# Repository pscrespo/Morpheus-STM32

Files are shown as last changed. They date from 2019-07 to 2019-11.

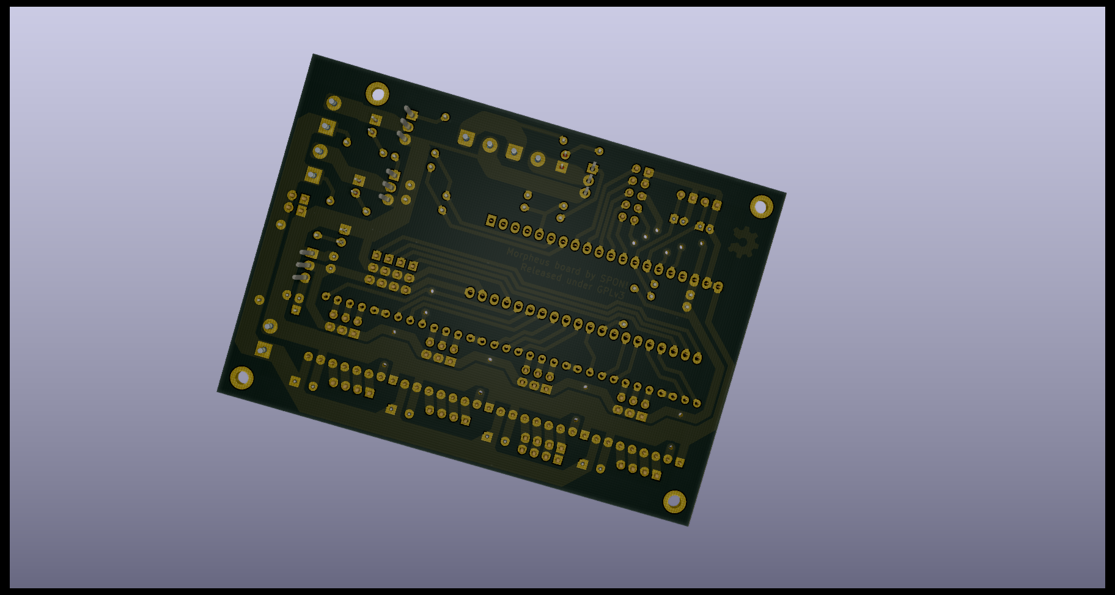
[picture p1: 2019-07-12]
documents/render3.png

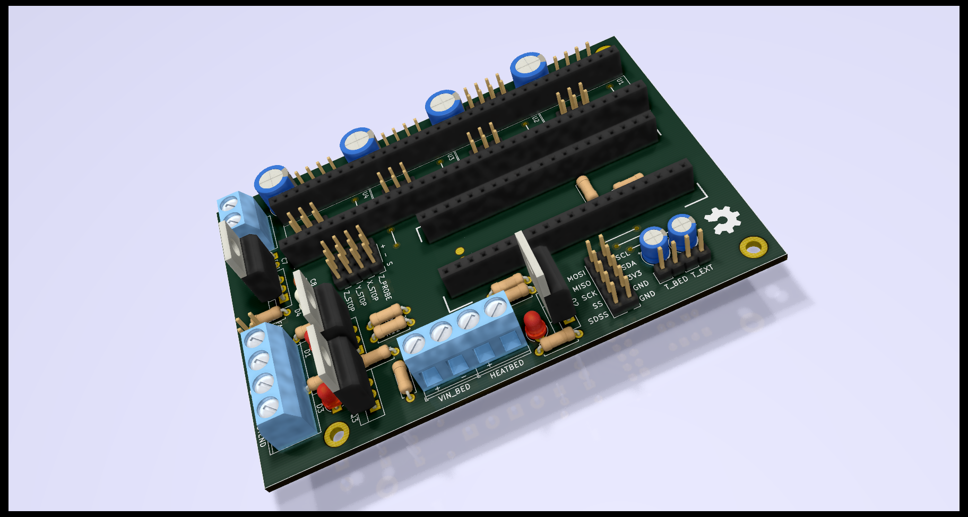
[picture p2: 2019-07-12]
documents/render2.png

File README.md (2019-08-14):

# Morpheus-STM32 (work in progress)
A cheap 3D printer controller board for use with a "Blue Pill" STM32F1 generic board. Inspired on http://reprap.org/wiki/SinapTec

Design goals:
---------------

 - Follow the [KISS Principle](https://en.wikipedia.org/wiki/KISS_principle)
 - Low cost
 - Single layer copper board
 - DIY-able (easy to make via toner transfer)
 - Only through-hole components
 - The very basic a printer would need
   - Keep bed circuit separated/optional (if you are making a PLA only printer without a heated bed, you don't need to populate the bed circuit zone)
 - Open Source Hardware, made in Open Source Software

Features:
---------------

 - 4 Pololu-like steppers (X, Y, Z, E0)
 - 3 mosfets (Hotend heater, print cooling fan and bed heater)
 - 3 MIN endstops (X, Y, Z)
 - Z Probe pin (in case you are building a delta printer and need the extra endstop)
 - 2 thermistors (for E0 and bed)
 - 2 12V fan connectors
 - I2C and SPI header
  
 # WARNING:
 - All logic voltage in this board is 3.3V. Do not connect 5V logic addons/devices without proper level adapting.
 - ~This board has no reverse current protection,~ it has a diode to short-circuit and protect the board in case of reverse current, but if you connect power incorrectly you'll still damage components and/or your power supply (there's also a risk of caching fire, so please be careful).
 - This board has no overcurrent protection, please use a fuse on power input (e.g. auto-blade or inline fuse holder), recommended values are of 5A for the main board and 10A for the bed circuit.
 - Check all connections before plugging power.
 - Now for real, check connections...
 
 Notes:
 ---------------
 - Usually, "blue pill" boards have a wrong R10 value (USB pullpup resistor, should be 1.5k but manufcturers place a 10k or other value resistor instead), so you can add a 1.8k in R13. If your board has the correct value or you already fixed it in the board, then leave R13 unpopulated.
 - ~Hotend sensor uses a 1k resistor pullup (R1). Anyway, if you're having trouble with finding (or creating) thermistor tables, just replace it with a 4.7k resistor and use the usual Marlin tables.~ 
  Now Marlin has configurable thermistors, you can use thermistor **1000** in **configuration.h** and choose pull-up, ressistance and beta values in **configuration_adv.h**

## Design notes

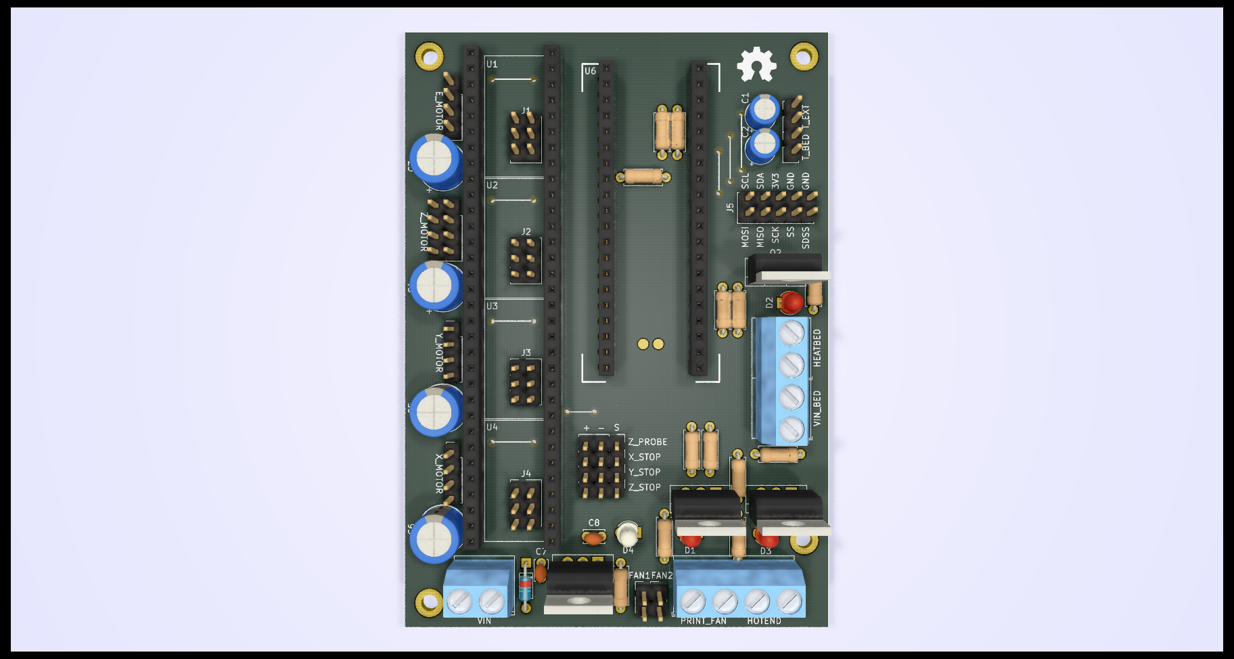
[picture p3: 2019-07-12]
documents/render1.png

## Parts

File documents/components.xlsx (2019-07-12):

Reference | Quantity | Value | Footprint | Notes
C1 C2 | 2 | 10uF10v | Capacitor_THT:CP_Radial_D5.0mm_P2.00mm
C3 C4 C5 C6 | 4 | 470uF16v | Capacitor_THT:CP_Radial_D8.0mm_P3.80mm
C7 C8 | 2 | 0.1uF | Capacitor_THT:C_Disc_D3.4mm_W2.1mm_P2.50mm
D1 D2 D3 | 3 | LED 3mm (Red) | LED_THT:LED_D3.0mm
D4 | 1 | LED 3mm (Green) | LED_THT:LED_D3.0mm_Clear
D5 | 1 | 1N4007 | Diode_THT:D_DO-35_SOD27_P7.62mm_Horizontal
HEATBED1 HOTEND1 PRINT_FAN1 VIN1 VIN_BED1 | 5 | Phoenix MKDS-1,5 2pin | TerminalBlock_Phoenix:TerminalBlock_Phoenix_MKDS-1,5-2_1x02_P5.00mm_Horizontal
Q1 Q3 | 2 | IRLZ44N | Package_TO_SOT_THT:TO-220-3_Vertical
Q2 | 1 | IRLB3034PBF | Package_TO_SOT_THT:TO-220-3_Vertical
R1 R3 R6 R9 | 4 | 1K | Resistor_THT:R_Axial_DIN0207_L6.3mm_D2.5mm_P7.62mm_Horizontal
R12 R2 | 2 | 4K7 | Resistor_THT:R_Axial_DIN0207_L6.3mm_D2.5mm_P7.62mm_Horizontal
R13 | 1 | 1K8 | Resistor_THT:R_Axial_DIN0207_L6.3mm_D2.5mm_P7.62mm_Horizontal | May be a different value for your bluepill, or not even needed.
R10 R4 R7 | 3 | 10R | Resistor_THT:R_Axial_DIN0207_L6.3mm_D2.5mm_P7.62mm_Horizontal
R11 R5 R8 | 3 | 100K | Resistor_THT:R_Axial_DIN0207_L6.3mm_D2.5mm_P7.62mm_Horizontal
T_BED1 T_EXT1 FAN1 FAN2 | 4 | Male header 01x02 | Connector_PinHeader_2.54mm:PinHeader_1x02_P2.54mm_Vertical | There are 74 pins in total, so you need 2 40pin header strips.
J1 J2 J3 J4 | 4 | Male header 02x03 | Connector_PinHeader_2.54mm:PinHeader_2x03_P2.54mm_Vertical
J5 | 1 | Male header 02x05 | Connector_PinHeader_2.54mm:PinHeader_2x05_P2.54mm_Vertical
X_STOP1 Y_STOP1 Z_STOP1 Z_PROBE1 | 4 | Male header 01x03 | Connector_PinHeader_2.54mm:PinHeader_1x03_P2.54mm_Vertical
X_MOTOR1 Y_MOTOR1 Z_MOTOR1 Z_MOTOR2 E_MOTOR1 | 5 | Male header 01x04 | Connector_PinHeader_2.54mm:PinHeader_1x04_P2.54mm_Vertical
U1 U2 U3 U4 | 4 | Pololu Driver | Module:Pololu_Breakout-16_15.2x20.3mm | This would be 4 40pin female header strips, but you can get away with 3.
U6 | 1 | BluePill_STM32F103C | Footprint based on the one made by www.rogerclark.net
U5 | 1 | LM1117-3.3 | Package_TO_SOT_THT:TO-220-3_Vertical | Consider using a heatsink for this.

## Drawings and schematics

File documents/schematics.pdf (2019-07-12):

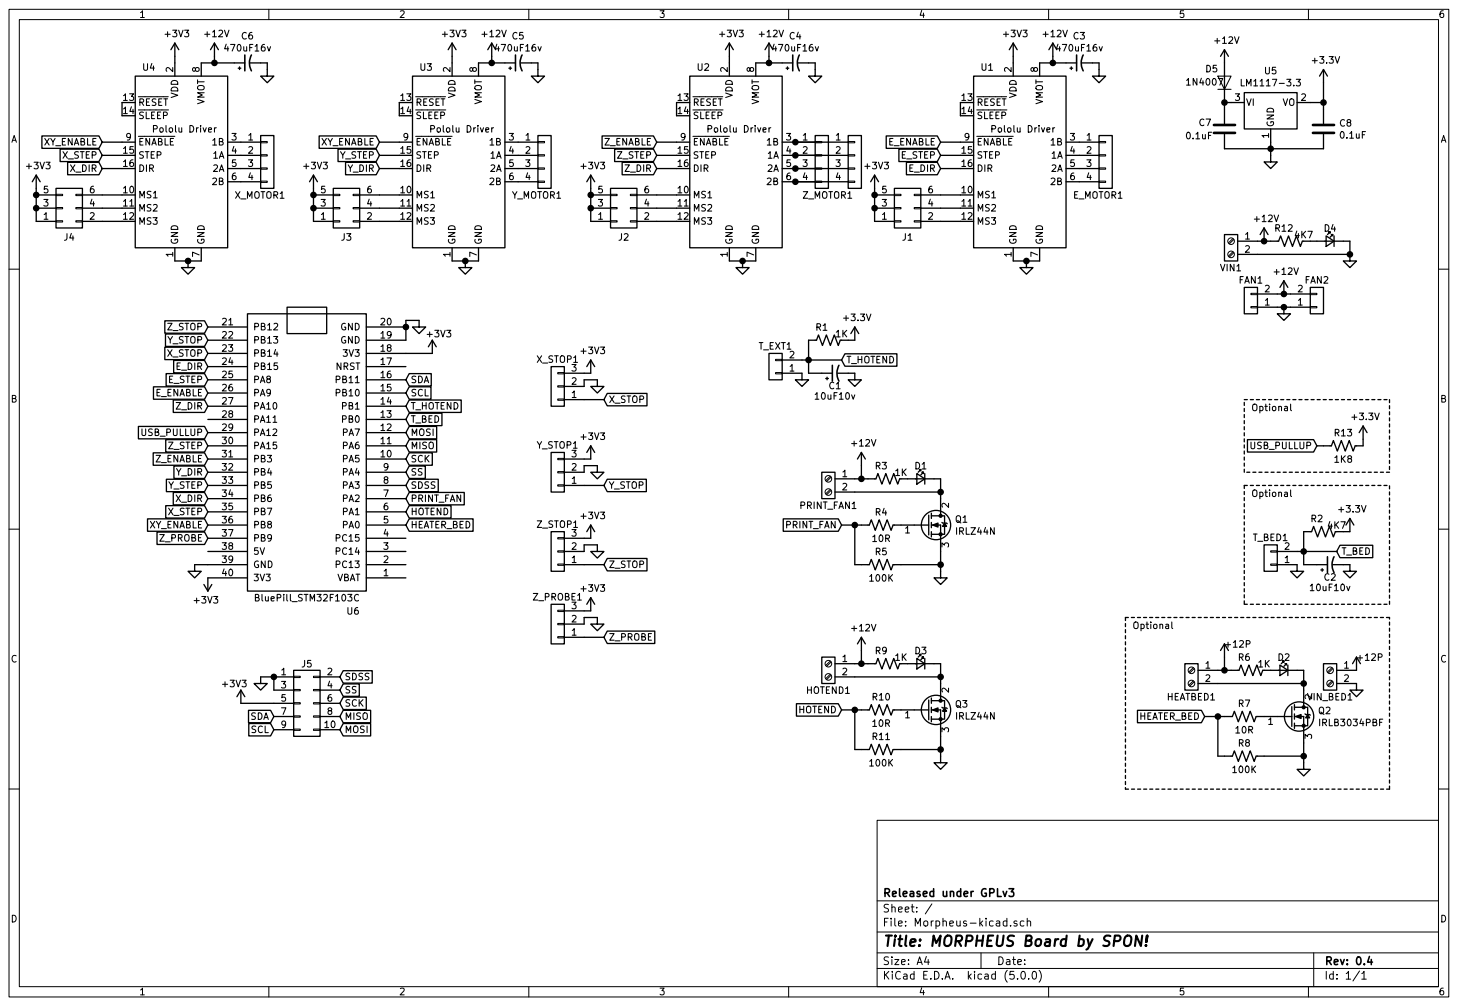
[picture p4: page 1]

1 MS1 10 MS2 11 MS3 12 RESET 13 SLEEP 14 STEP 15 DIR 16 VDD

File: Morpheus-kicad.sch Sheet: / Released under GPLv3 GND

Id: 1/1 Title: MORPHEUS Board by SPON!

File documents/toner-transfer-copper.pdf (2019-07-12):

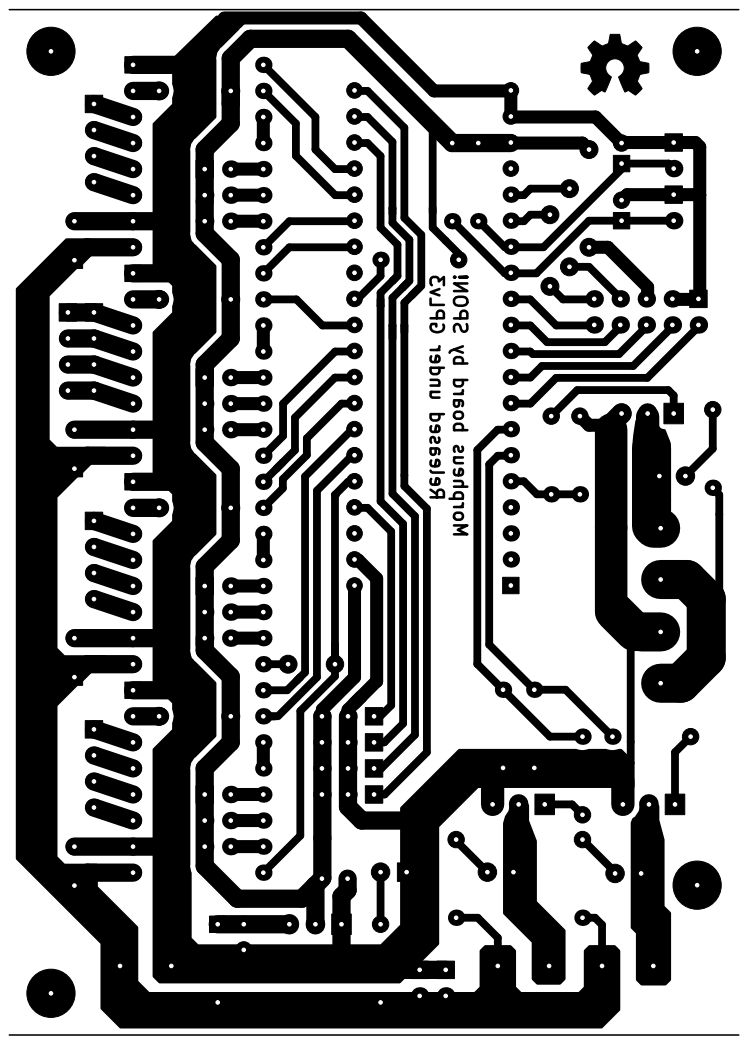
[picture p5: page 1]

Released under GPLv3 Morpheus board by SPON!

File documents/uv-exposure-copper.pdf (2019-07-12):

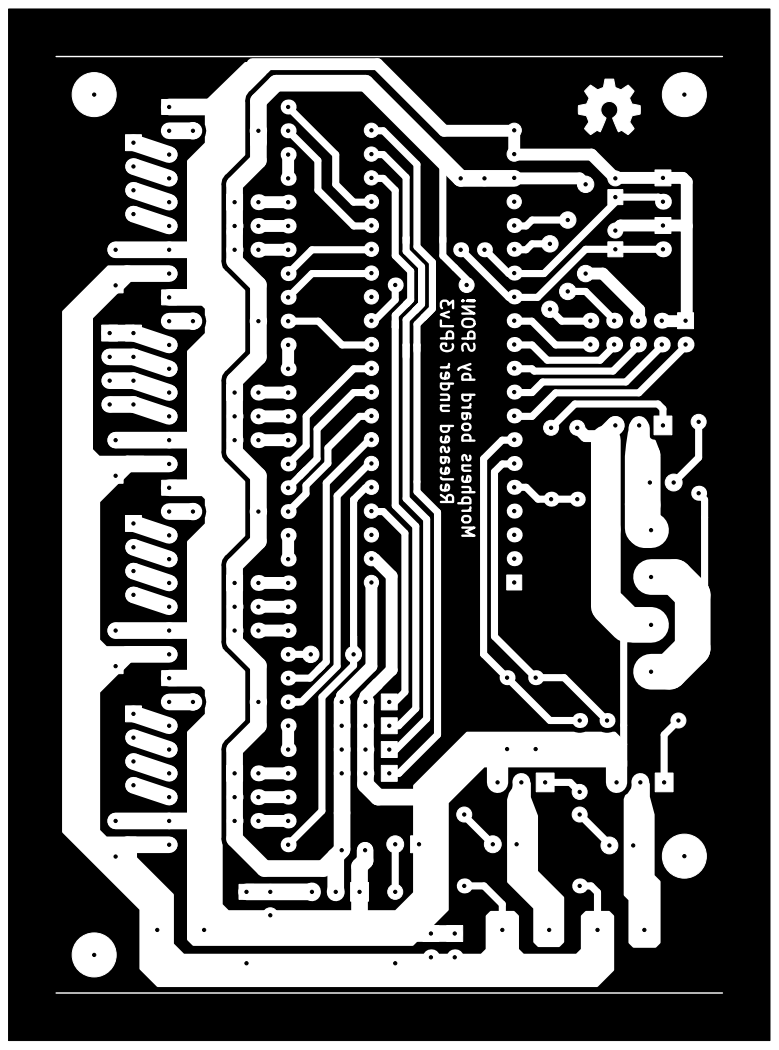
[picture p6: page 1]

Released under GPLv3 Morpheus board by SPON!

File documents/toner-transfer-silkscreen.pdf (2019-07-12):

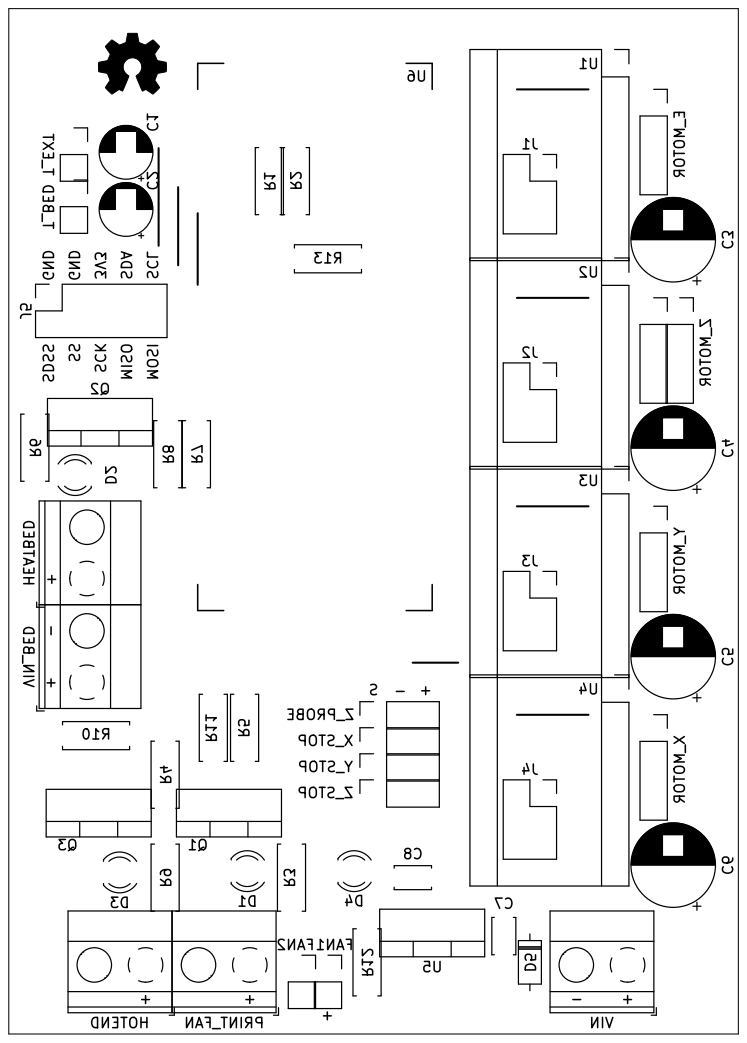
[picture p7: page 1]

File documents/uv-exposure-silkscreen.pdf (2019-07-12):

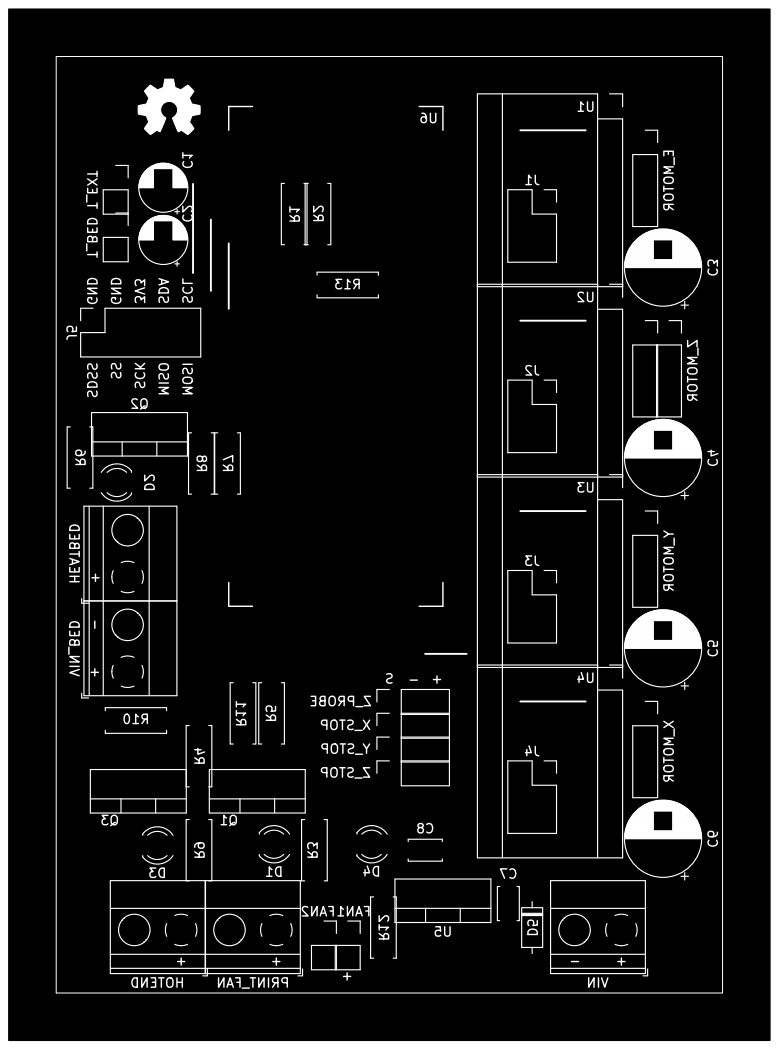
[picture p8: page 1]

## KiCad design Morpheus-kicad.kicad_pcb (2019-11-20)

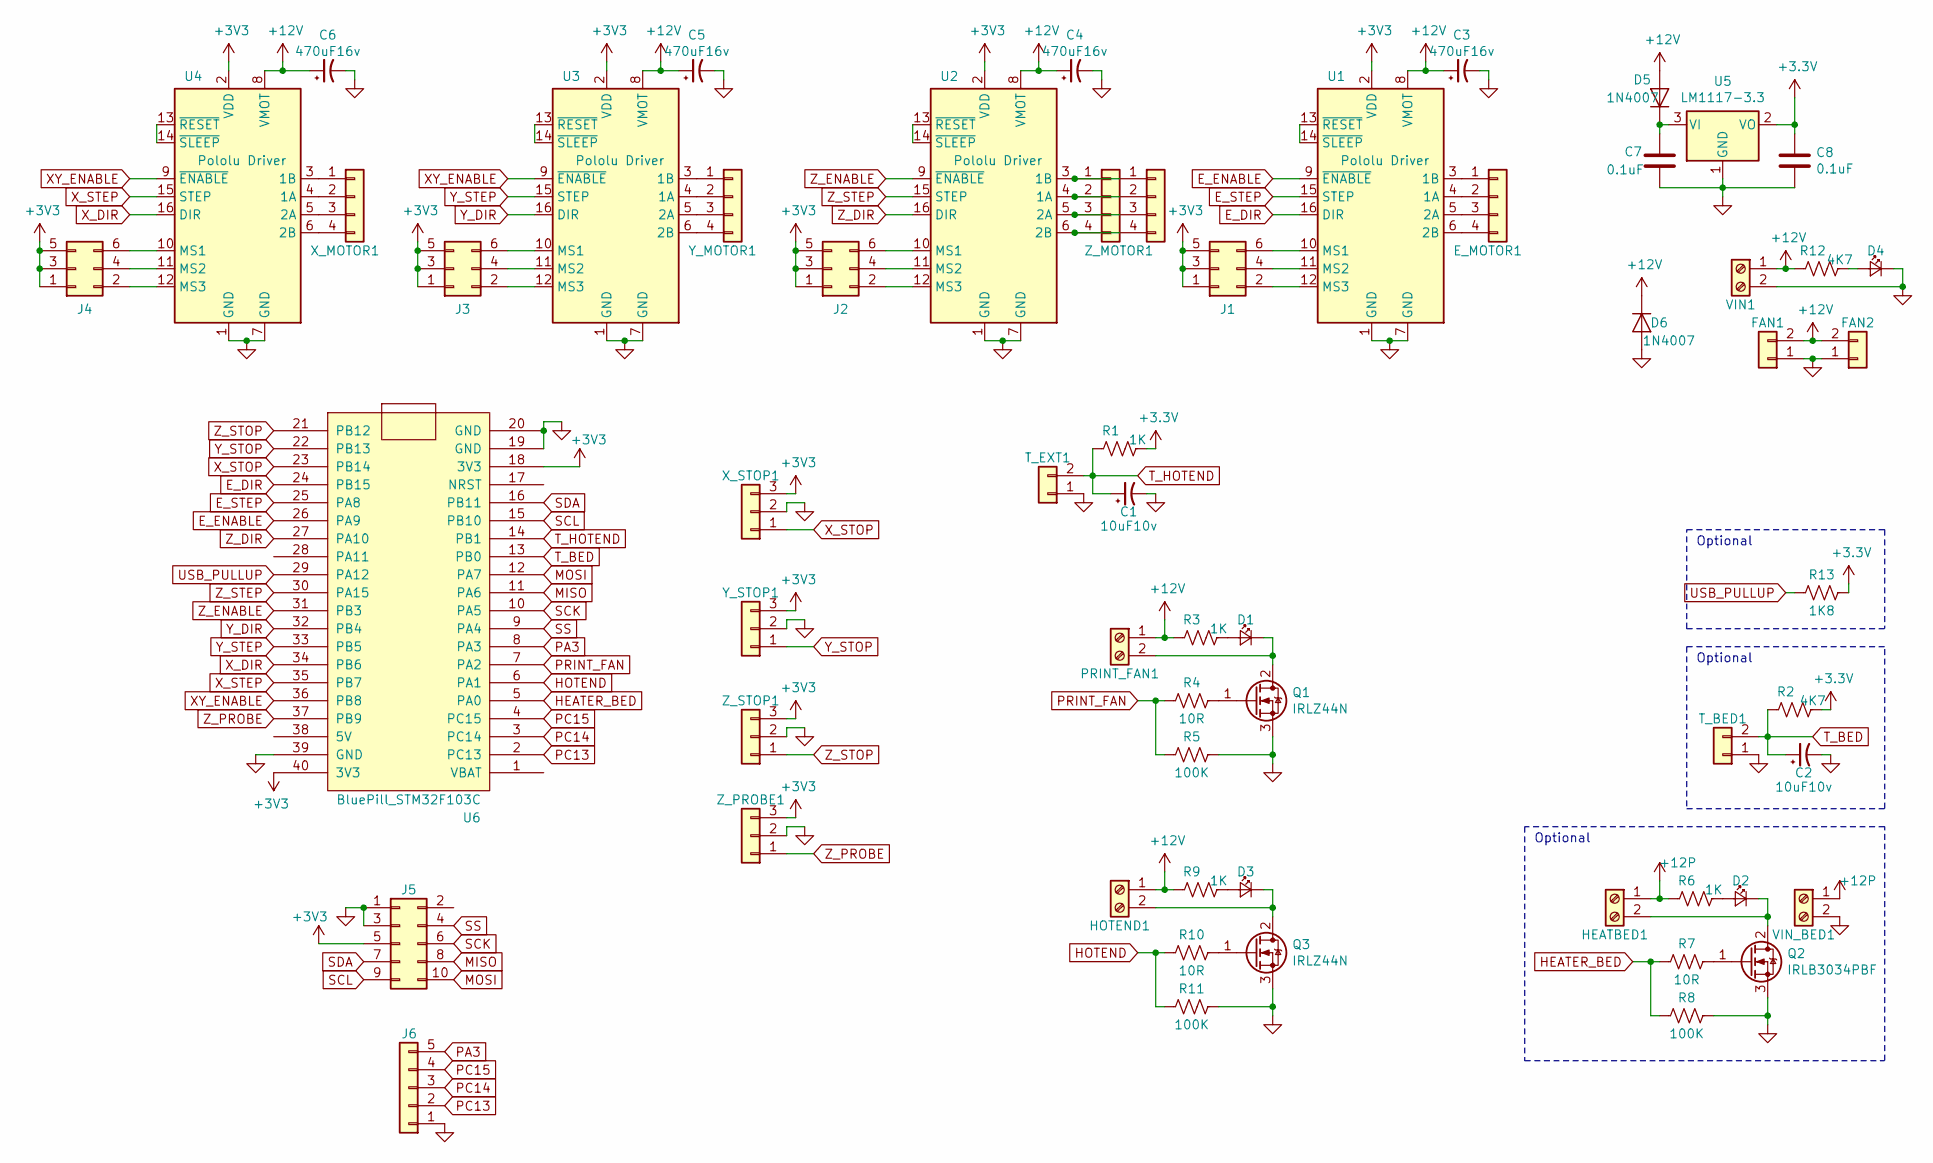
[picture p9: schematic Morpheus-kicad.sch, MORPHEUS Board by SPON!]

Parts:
C1, C2: 10uF10v; CP_Radial_D5.0mm_P2.00mm
C3, C4, C5, C6: 470uF16v; CP_Radial_D8.0mm_P3.80mm
C7, C8: 0.1uF; C_Disc_D3.4mm_W2.1mm_P2.50mm
D1, D2, D3: LED_Small; LED_D3.0mm
D4: LED_Small; LED_D3.0mm_Clear
D5: 1N4007; D_DO-35_SOD27_P7.62mm_Horizontal
D6: 1N4007; D_DO-35_SOD27_P2.54mm_Vertical_AnodeUp
E_MOTOR1: E_MOTOR; PinHeader_1x04_P2.54mm_Vertical
FAN1, FAN2: Conn_01x02; PinHeader_1x02_P2.54mm_Vertical
HEATBED1: HEATBED; TerminalBlock_Phoenix_MKDS-1,5-2_1x02_P5.00mm_Horizontal
HOTEND1: HOTEND; TerminalBlock_Phoenix_MKDS-1,5-2_1x02_P5.00mm_Horizontal
J1, J2, J3, J4: Conn_02x03_Odd_Even; PinHeader_2x03_P2.54mm_Vertical
J5: Conn_02x05_Counter_Clockwise; PinHeader_2x05_P2.54mm_Vertical
J6: Conn_01x05; PinHeader_1x05_P2.54mm_Vertical
PRINT_FAN1: PRINT_FAN; TerminalBlock_Phoenix_MKDS-1,5-2_1x02_P5.00mm_Horizontal
Q1, Q3: IRLZ44N; TO-220-3_Vertical
Q2: IRLB3034PBF; TO-220-3_Vertical
R1, R3, R6, R9: 1K; R_Axial_DIN0207_L6.3mm_D2.5mm_P7.62mm_Horizontal
R2, R12: 4K7; R_Axial_DIN0207_L6.3mm_D2.5mm_P7.62mm_Horizontal
R4, R7, R10: 10R; R_Axial_DIN0207_L6.3mm_D2.5mm_P7.62mm_Horizontal
R5, R8, R11: 100K; R_Axial_DIN0207_L6.3mm_D2.5mm_P7.62mm_Horizontal
R13: 1K8; R_Axial_DIN0207_L6.3mm_D2.5mm_P7.62mm_Horizontal
T_BED1: T_BED; PinHeader_1x02_P2.54mm_Vertical
T_EXT1: T_EXT; PinHeader_1x02_P2.54mm_Vertical
U1, U2, U3, U4: Pololu Driver; Pololu_Breakout-16_15.2x20.3mm
U5: LM1117-3.3; TO-220-3_Vertical
U6: BluePill_STM32F103C
VIN1: VIN; TerminalBlock_Phoenix_MKDS-1,5-2_1x02_P5.00mm_Horizontal
VIN_BED1: VIN_BED; TerminalBlock_Phoenix_MKDS-1,5-2_1x02_P5.00mm_Horizontal
X_MOTOR1: X_MOTOR; PinHeader_1x04_P2.54mm_Vertical
X_STOP1: X_STOP; PinHeader_1x03_P2.54mm_Vertical
Y_MOTOR1: Y_MOTOR; PinHeader_1x04_P2.54mm_Vertical
Y_STOP1: Y_STOP; PinHeader_1x03_P2.54mm_Vertical
Z_MOTOR1: Z_MOTOR; PinHeader_1x04_P2.54mm_Vertical
Z_MOTOR2: Conn_01x04; PinHeader_1x04_P2.54mm_Vertical
Z_PROBE1: Z_PROBE; PinHeader_1x03_P2.54mm_Vertical
Z_STOP1: Z_STOP; PinHeader_1x03_P2.54mm_Vertical

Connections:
+12P: HEATBED1.1, R6.2, VIN_BED1.1
+12V: C3.1, C4.1, C5.1, C6.1, D5.2 (A), D6.1 (K), FAN1.2, FAN2.2, HOTEND1.1, PRINT_FAN1.1, R3.2, R9.2, R12.2, U1.8 (VMOT), U2.8 (VMOT), U3.8 (VMOT), U4.8 (VMOT), VIN1.1
E_DIR: U1.16 (DIR), U6.24 (PB15)
E_ENABLE: U1.9 (~ENABLE), U6.26 (PA9)
E_STEP: U1.15 (STEP), U6.25 (PA8)
GND: C1.2, C2.2, C3.2, C4.2, C5.2, C6.2, C7.2, C8.2, D4.1 (K), D6.2 (A), FAN1.1, FAN2.1, J5.1, J5.3, J6.1, Q1.3 (S), Q2.3 (S), Q3.3 (S), R5.1, R8.1, R11.1, T_BED1.1, T_EXT1.1, U1.1 (GND), U1.7 (GND), U2.1 (GND), U2.7 (GND), U3.1 (GND), U3.7 (GND), U4.1 (GND), U4.7 (GND), U5.1 (GND), U6.19 (GND), U6.20 (GND), U6.39 (GND), VIN1.2, VIN_BED1.2, X_STOP1.2, Y_STOP1.2, Z_PROBE1.2, Z_STOP1.2
HEATER_BED: R7.2, R8.2, U6.5 (PA0)
HOTEND: R10.2, R11.2, U6.6 (PA1)
MISO: J5.8, U6.11 (PA6)
MOSI: J5.10, U6.12 (PA7)
unnamed: C7.1, D5.1 (K), U5.3 (VI)
unnamed: D1.1 (K), PRINT_FAN1.2, Q1.2 (D)
unnamed: D1.2 (A), R3.1
unnamed: D2.1 (K), HEATBED1.2, Q2.2 (D)
unnamed: D2.2 (A), R6.1
unnamed: D3.1 (K), HOTEND1.2, Q3.2 (D)
unnamed: D3.2 (A), R9.1
unnamed: D4.2 (A), R12.1
unnamed: E_MOTOR1.1, U1.3 (1B)
unnamed: E_MOTOR1.2, U1.4 (1A)
unnamed: E_MOTOR1.3, U1.5 (2A)
unnamed: E_MOTOR1.4, U1.6 (2B)
unnamed: J1.2, U1.12 (MS3)
unnamed: J1.4, U1.11 (MS2)
unnamed: J1.6, U1.10 (MS1)
unnamed: J2.2, U2.12 (MS3)
unnamed: J2.4, U2.11 (MS2)
unnamed: J2.6, U2.10 (MS1)
unnamed: J3.2, U3.12 (MS3)
unnamed: J3.4, U3.11 (MS2)
unnamed: J3.6, U3.10 (MS1)
unnamed: J4.2, U4.12 (MS3)
unnamed: J4.4, U4.11 (MS2)
unnamed: J4.6, U4.10 (MS1)
unnamed: Q1.1 (G), R4.1
unnamed: Q2.1 (G), R7.1
unnamed: Q3.1 (G), R10.1
unnamed: U1.13 (~RESET), U1.14 (~SLEEP)
unnamed: U2.3 (1B), Z_MOTOR1.1, Z_MOTOR2.1
unnamed: U2.4 (1A), Z_MOTOR1.2, Z_MOTOR2.2
unnamed: U2.5 (2A), Z_MOTOR1.3, Z_MOTOR2.3
unnamed: U2.6 (2B), Z_MOTOR1.4, Z_MOTOR2.4
unnamed: U2.13 (~RESET), U2.14 (~SLEEP)
unnamed: U3.3 (1B), Y_MOTOR1.1
unnamed: U3.4 (1A), Y_MOTOR1.2
unnamed: U3.5 (2A), Y_MOTOR1.3
unnamed: U3.6 (2B), Y_MOTOR1.4
unnamed: U3.13 (~RESET), U3.14 (~SLEEP)
unnamed: U4.3 (1B), X_MOTOR1.1
unnamed: U4.4 (1A), X_MOTOR1.2
unnamed: U4.5 (2A), X_MOTOR1.3
unnamed: U4.6 (2B), X_MOTOR1.4
unnamed: U4.13 (~RESET), U4.14 (~SLEEP)
PA3: J6.5, U6.8 (PA3)
PC13: J6.2, U6.2 (PC13)
PC14: J6.3, U6.3 (PC14)
PC15: J6.4, U6.4 (PC15)
PRINT_FAN: R4.2, R5.2, U6.7 (PA2)
SCK: J5.6, U6.10 (PA5)
SCL: J5.9, U6.15 (PB10)
SDA: J5.7, U6.16 (PB11)
SS: J5.4, U6.9 (PA4)
T_BED: C2.1, R2.2, T_BED1.2, U6.13 (PB0)
T_HOTEND: C1.1, R1.2, T_EXT1.2, U6.14 (PB1)
USB_PULLUP: R13.2, U6.29 (PA12)
XY_ENABLE: U3.9 (~ENABLE), U4.9 (~ENABLE), U6.36 (PB8)
X_DIR: U4.16 (DIR), U6.34 (PB6)
X_STEP: U4.15 (STEP), U6.35 (PB7)
X_STOP: U6.23 (PB14), X_STOP1.1
Y_DIR: U3.16 (DIR), U6.32 (PB4)
Y_STEP: U3.15 (STEP), U6.33 (PB5)
Y_STOP: U6.22 (PB13), Y_STOP1.1
Z_DIR: U2.16 (DIR), U6.27 (PA10)
Z_ENABLE: U2.9 (~ENABLE), U6.31 (PB3)
Z_PROBE: U6.37 (PB9), Z_PROBE1.1
Z_STEP: U2.15 (STEP), U6.30 (PA15)
Z_STOP: U6.21 (PB12), Z_STOP1.1

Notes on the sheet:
Optional

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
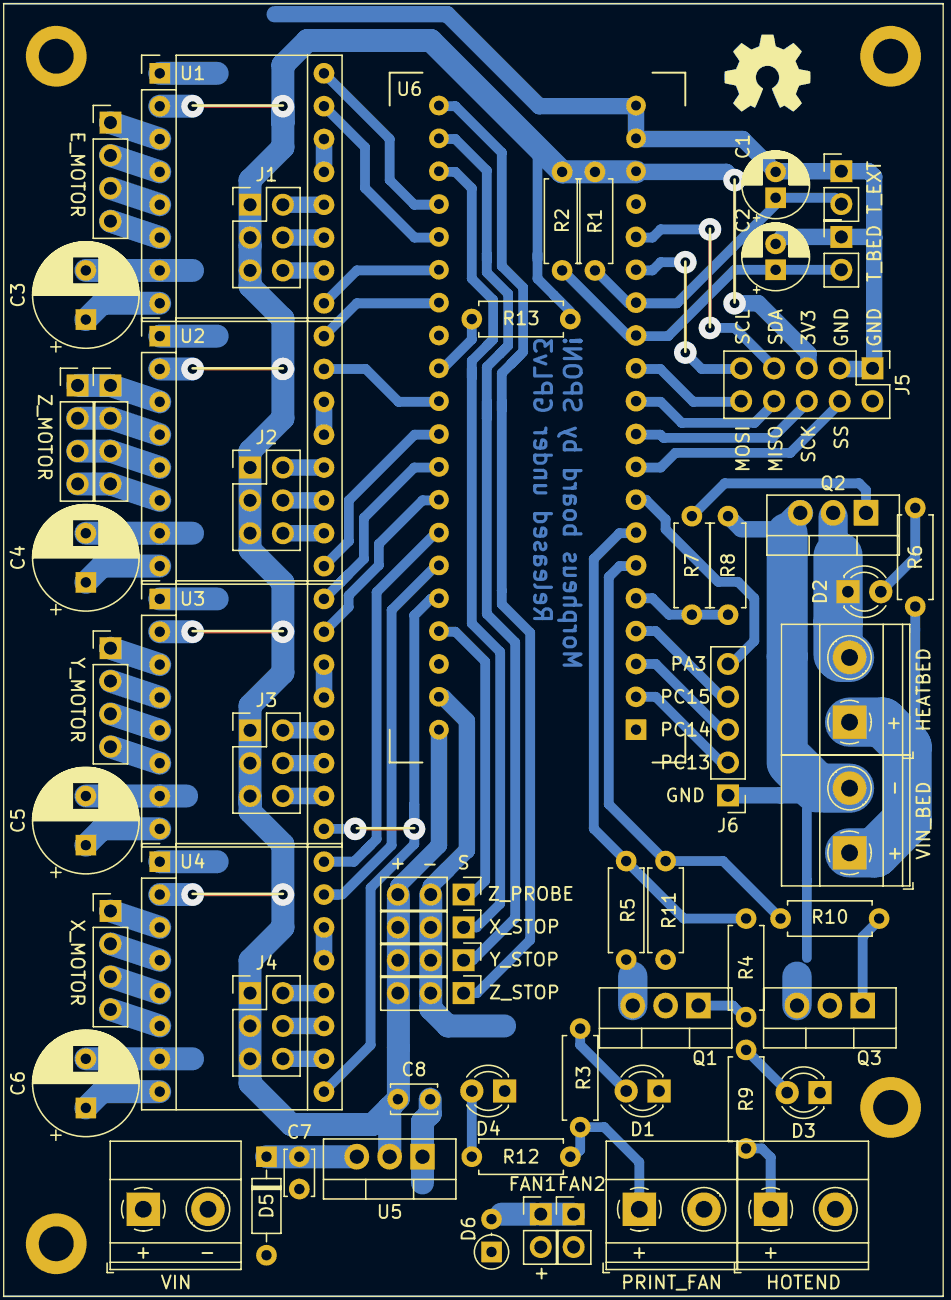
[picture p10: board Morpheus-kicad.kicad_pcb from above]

Board: 2 copper layers, 60 parts (0 on the bottom side), 78 nets.

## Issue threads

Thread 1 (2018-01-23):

Work status?

dossalab, 2018-01-23:
Hi, I'm really interested in this project. Blue pill is a cheap and powerful board, so it's a nice choice for 3d printers. So I want to know is this board complete? Can I make one? Which software works with your board?

pscrespo, 2018-01-23:
Hello. I didn't make one yet, you can make one if you want. Please consider that this project is a work in progress, and it may have some mistake that I didn't see yet. Also this board has no fuses or reverse current protection, please make sure that all cables are connected properly and use an external fuse. As of firmware, I'm waiting for a functional Marlin release (you can track it too here: "https://github.com/MarlinFirmware/Marlin/issues/7076"). I'm hoping that Marlin works with STM32F1 boards since it would be a very cheap upgrade to 32bits, especially for delta machines.

jakep82, 2018-07-06:
Klipper supports the STM32 board.

[https://github.com/KevinOConnor/klipper/blob/master/docs/Features.md](url)

vivian-ng, 2018-10-24:
Can I clarify if the diode beside the VIN is to guard against reverse polarity?

Also, is there a list of components (capacitors, resistors, MOSFETs, etc.) that is needed? Or do I just RTFM (or in this case, RTFPDF)?

pscrespo, 2018-10-27:
Hi! The diode is needed because when tested with USB voltage input only, there was current on 12V rails, apprently due to how the LM1117 works. Currently it has no reverse polarity or overcurrent protection. Also I found that HW PWM is not working correctly yet on Marlin 2.0 so print fan doesn't work as intended.
As for the BOM, I'll make one soon so it's easier for you.
@jakep82 I've been reading about Klipper, it's really nice but my goal for now it's to make it work correctly with Marlin. If you want to try it would be nice to see how it performs.

jakep82, 2018-10-30:
I'm interested in building one as soon as a BOM is available. I have a couple STM32 Dev boards, and I want to test this board with Klipper for a future printer.

Alfrederson, 2019-02-04:
Did you managed to get the built-in USB port when compiling Marlin 2.0?

Vicbarn, 2019-07-08:
Hi. I got Marlin 2 compiled with Arduino IDE and fully working on my Blue Pill board.

The latest Arduino 1.8.9 with updated boards STM32 Cores ver. 1.6.1 updated using Additional boards in preferences with https://github.com/stm32duino/BoardManagerFiles/raw/master/STM32/package_stm_index.json allowed me to select under tools:
Board: Generic STM32F1 Series
Board part number: Bluepill F103C8 (128k)
U(S)ART support "Enabled (generic 'Serial')"
USB support (if available): "CDC (generic 'Serial' supersede U(S)ART"

I copied just the Marlin folder from Marlin-bugfix-2.0.x to my Arduino Projects folder. I opened the .ino file from Ardiuno IDE and selected my board as above.
Using the default Configuration files I chose
#define SERIAL_PORT 1
#define SERIAL_PORT_2 -1
giving me both Blue Pill Serial 1 on PA 9 and PA10, and USB serial working.
I chose #define MOTHERBOARD BOARD_MALYAN_M200 as my motherboard.
This compiled without any errors or warnings and uploaded the firmware to my Blue Pill using ST-Link V2
I connected XYZ Min, A15, B4 and B5 to 3.3v and A0 (T0 sensor) to a 10k Potentiometer between gnd and 3.3V to set its voltage for 210 C. This was necessary to stop Marlin from performing a critical Halt for Thermal runaway etc. I then connected via USB to Repetier Host after installing the STM32 VCP serial driver available at https://www.st.com/en/development-tools/stsw-stm32102.html.

I was able to serial connect to Blue Pill from Repetier and load, slice and print a model to it. I checked all the pins with an oscilloscope and all signals were exactly as expected.

Choosing #define MOTHERBOARD BOARD_MORPHEUS gave errors and after editing lines producing errors in the pins_MORPHEUS.h file I managed to compile and upload but the Blue Pill went into a Watchdog reset every 4 seconds. This is because of a pins - timer usage clash.

@pscrespo Please change your pins_MORPHEUS.h file to get a pins combination that doesn't produce a timer clash and if possible make PA9 and PA10 available for a serial WIFI connection.

Your work is much appreciated and I look forward to a final PCB to plug my Blue Pill into and to start printing!

Vicbarn, 2019-07-15:
Hi pscrespo
Thank you very much for your board and pins update. In order to get a successful build I had to use Arduino IDE with modified MalyanM200 pins to match Morpheus. I would love to use PlatformIO but haven't managed a successful build. Could you please add your platformio.ini, Configuration_.h and Configuration_adv.h files to the code section to help me build using PlatformIO.

Cleric-K, 2019-12-11:
Here's my recipe for building with PlatformIO:

1. Use the latest `2.0.x` branch of Marlin.
2. Create new environment in `platformio.ini`
```ini
[env:STM32F103CB_morpheus]
platform    = ststm32
board       = genericSTM32F103CB
build_flags = !python Marlin/src/HAL/HAL_STM32F1/build_flags.py -ffunction-sections -fdata-sections -Wl,--gc-sections
src_filter  = ${common.default_src_filter} +<src/HAL/HAL_STM32F1>
lib_ignore  = Adafruit NeoPixel, LiquidCrystal, LiquidTWI2, TMCStepper, U8glib-HAL, SPI
```
3. Optionally modify:
```ini
[platformio]
...
default_envs = STM32F103CB_morpheus
```
4. The minimum changes to `Configuration.h` are:
```c
#define SERIAL_PORT -1
```
and
```c
#define MOTHERBOARD BOARD_MORPHEUS
```
5. Build and flash!

Seems to work, responds correctly in Pronterface. On Windows I had to install the drivers for the Maple USB serial port:
`~/.platformio/packages/framework-arduinoststm32-maple/drivers/win/install_drivers.bat`

Note that the above configuration builds image for direct flashing (stlink), and not for stm32duino/maple bootloader. It seems that PlatformIO has some hardcoded preferences for the linker script (which determines the type of image to build) according to the name of the board (see `~/.platformio/packages/framework-arduinoststm32-maple/tools/platformio-build-stm32f1.py`).

If you would like to build version for flashing with the bootloader, you have to use env such as this:
```ini
[env:STM32F103CB_morpheus]
platform    = ststm32
board       = bluepill_f103c8_128k
board_build.core = maple
build_flags = !python Marlin/src/HAL/HAL_STM32F1/build_flags.py -ffunction-sections -fdata-sections -Wl,--gc-sections
src_filter  = ${common.default_src_filter} +<src/HAL/HAL_STM32F1>
lib_ignore  = Adafruit NeoPixel, LiquidCrystal, LiquidTWI2, TMCStepper, U8glib-HAL, SPI
```

The `platformio-build-stm32f1.py` scripts builds bootloader code (code at `0x8002000`) for the `bluepill_f103c8_128k` board and raw code (at `0x8000000`) for the `genericSTM32F103CB` board.

Vicbarn, 2019-12-12:
@Cleric-K
Hi. Thanks a stack for the PlatformIO instructions. Worked perfectly!
Trying to get OpenOCD in PlatformIO to upload via Stlink to a Blue Pill board with 128k ROM but reporting as 64K . OpenOCD has a size overide option, but I need to find where to do this. Another option is to use STM32CubeProgrammer like Arduino does. Arduino happily programs the board. Would be great if you could help. My IDE environment experience is rather low.

Cleric-K, 2019-12-12:
Unfortunately I don't have elegant solution to this one. What I do is to manually edit:
`~\.platformio\packages\tool-openocd\scripts\target\stm32f1x.cfg`
and replace `$_FLASH_SIZE` on the `flash bank ...` line with sufficiently large number, for eaxmple `0x1000000`. We are not setting it to `0x20000` (128K) because that would restrict flashing _other_ f1xx MCUs which might have more than that:

`flash bank $_FLASHNAME stm32f1x 0x08000000 0x10000000 0 $_TARGETNAME`

The above number will allow OpenOCD to _try_ to flash images up to 16MB. It will fail of course, but I don't think this can do any harm (besides leaving the mcu in unworkable state).

Vicbarn, 2019-12-12:
Thanks
Tiny typo. Used
flash bank $_FLASHNAME stm32f1x 0x08000000 0x1000000 0 0 $_TARGETNAME
Worked perfectly.

Cleric-K, 2019-12-13:
Just for the record, here's also how to use STLink (no changes in `.cfg` scripts needed). This must be added to the `[env...]` section:

```ini
upload_protocol = custom
upload_command = $PROJECT_PACKAGES_DIR/tool-stm32duino/stlink/ST-LINK_CLI.exe -ME -V -P $SOURCE 0x8000000 -Rst
```

Vicbarn, 2019-12-14:
Thanks. Worked!

pebri86, 2019-12-17:
Thanks. Did anyone tried enabled sdsupport? Is it fit on 128kb flash?

Cleric-K, 2019-12-17:
Quick test with SD enabled caused overflow with about +13KB.

I think I'm missing something. Then I compiled the same config for arduino 128 and the bin is just 66K! I'm not very experienced with the Marlin code but I suspect that the stm32 version compiles unnecessary stuff.

pscrespo, 2019-12-17:
Hi there! First, thanks to everyone, it's great to see users helping others! I apologize for not being around lately, I'm going to make some time to write a (simple and short) tutorial in the wiki, but for now, to save space you can:
- Comment #define ARC_SUPPORT in Configuration_adv.h
- Uncomment #define NO_VOLUMETRICS in Configuration_adv.h
- Uncomment #define SLIM_LCD_MENUS in Configuration.h

That will give enough space for LCD and SD support
If you need an extra you can:
- Comment #define SHOW_BOOTSCREEN in Configuration.h (~300B)
- Uncomment #define NO_WORKSPACE_OFFSETS in Configuration_adv.h (~1kB, but will change G92 behavior)

pebri86, 2019-12-18:
Using latest 2.0.x still overflowed ~3kb after disabled pid and even uncommenting #define NO_LCD_MENUS.

Vicbarn, 2019-12-19:
Built using Arduino IDE with SDSUPPORT enabled and it was successful with result:
Sketch uses 97576 bytes (74%) of program storage space. Maximum is 131072 bytes.
Global variables use 8144 bytes (39%) of dynamic memory, leaving 12336 bytes for local variables. Maximum is 20480 bytes.

Must use different libraries. Takes four times as long to build though!

pebri86, 2019-12-20:
@Vicbarn could you share what you have done? I failed to compile using Arduino IDE.

Vicbarn, 2019-12-20:
See my post on July 8th above. Need to use STM32 Cores ver. 1.6.1. The latest version may result in errors. Modified pins_MALYAN_M200.h below.
[pins_MALYAN_M200.zip](https://github.com/pscrespo/Morpheus-STM32/files/3987208/pins_MALYAN_M200.zip)

Vicbarn, 2019-12-20:
Rename pins_MALYAN_M200.zip to pins_MALYAN_M200.h.

pebri86, 2019-12-20:
@Vicbarn thanks it works. Compiled successfully SDSUPPORT enabled without LCD uses 88KB rom. I wonder why compiled with platformio so big binary size.

Vicbarn, 2019-12-20:
Hopefully @Cleric-K or @pscrespo will give us a new recipe for PlatformIO that will use the same libraries. I suspect the Arduino build uses custom HAL libraries instead of the STM HAL libraries.

pebri86, 2019-12-27:
Compile under Arduino IDE getting me serious pain, sometimes hangs or sometimes got filename too long. I manage to setting build flags platformio using arduino build flags. Here my settings
``` ini
#
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

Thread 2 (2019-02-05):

Schematic?

Alfrederson, 2019-02-05:
I etched this board just because, but what program do I use to open the .sch? It's not an Eagle .sch, and Altium Designer doesn't seem to be able to import it either

greboide, 2019-03-09:
aparently he is using gEDA suite

pscrespo, 2019-03-27:
@greboide That's correct. Current published version is made with gEDA. It's a little tricky to make it run in Windows but you can follow this guide: http://www.delorie.com/pcb/geda-windows/
I'm porting the board to KiCAD, wich is more used than gEDA these days, and is open source too.
@Alfrederson Schematic is here: https://github.com/pscrespo/Morpheus-STM32/blob/master/documents/morpheus.png

Closed 2019-07-12.

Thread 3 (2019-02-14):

TMC2130 Support

DragonHunter274, 2019-02-14:
Does this Board support the TMC2130 Silent StepSticks?

pscrespo, 2019-03-27:
I haven't tried Trinamic drivers, but if they support 3.3V Logic Voltage, should work fine. The board is not wired for a SPI connection to the drivers, so you'll have to connect them the same as pololu. Let me know if you try them.

Closed 2019-07-12.

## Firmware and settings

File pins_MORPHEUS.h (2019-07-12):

/**
 * Marlin 3D Printer Firmware
 * Copyright (C) 2019 MarlinFirmware [https://github.com/MarlinFirmware/Marlin]
 *
 * Based on Sprinter and grbl.
 * Copyright (C) 2011 Camiel Gubbels / Erik van der Zalm
 *
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
 */

 /**
  * 2017 Victor Perez Marlin for stm32f1 test
  * 2018 Modified by Pablo Crespo for Morpheus Board (https://github.com/pscrespo/Morpheus-STM32)
  */

/**
 * MORPHEUS Board pin assignments
 */

#ifndef __STM32F1__
  #error "Oops! Select an STM32F1 board in 'Tools > Board.'"
#endif

#define BOARD_NAME "Bluepill based board"

//
// Limit Switches
//
#define X_STOP_PIN         PB14
#define Y_STOP_PIN         PB13
#define Z_STOP_PIN         PB12

//
// Z Probe
//
#define Z_MIN_PROBE_PIN    PB9

//
// Steppers
//
// X & Y enable are the same
#define X_STEP_PIN         PB7
#define X_DIR_PIN          PB6
#define X_ENABLE_PIN       PB8

#define Y_STEP_PIN         PB5
#define Y_DIR_PIN          PB4
#define Y_ENABLE_PIN       PB8

#define Z_STEP_PIN         PA15
#define Z_DIR_PIN          PA10
#define Z_ENABLE_PIN       PB3

#define E0_STEP_PIN        PA8
#define E0_DIR_PIN         PB15
#define E0_ENABLE_PIN      PA9

//
// Temperature Sensors
//
#define TEMP_0_PIN         PB1   // Analog Input (HOTEND thermistor)
#define TEMP_BED_PIN       PB0   // Analog Input (BED thermistor)

//
// Heaters / Fans
//
#define HEATER_0_PIN       PA1   // HOTEND MOSFET
#define HEATER_BED_PIN     PA0   // BED MOSFET

#define FAN_PIN            PA2   // PRINT FAN

//
// Misc.
//
#define SDSS               PA3
#define SD_DETECT_PIN      -1
#define LED_PIN            PC13
#define DISABLE_JTAG
#define FAN_SOFT_PWM

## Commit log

2017-09-27 Initial release
    [morpheus.sch]
2017-10-02 Changed screw terminal footprints
    Changed screw terminal footprints, added silk lines to bridges, re-arranged bed circuit
2017-10-02 Added fan 12v connectors
    Added 2 fan connectors, one for extruder and an optional one for cooling the board.
    [morpheus.sch]
2017-10-09 Added I2C and SPI Header
    Added connector for external addons, which can use SPI and second I2C bus. Also updated readme file.
    [morpheus.sch]
2017-10-10 Added Z-probe and experimental pins.h file
    Added Z-probe (very useful in delta printers) and a basic pins.h file for experimenting with Marlin Firmware.
    [morpheus.sch]
2018-01-16 Caps corrected
    Corrected driver's capacitors to right size.
    Added OSHW logo :)
2018-05-18 Change Z-Probe pin
    X and Y enable now share the same pin.
    Z probe has a new pin.
    Reformatted pin definition file.
    [morpheus.sch]
2018-05-23 Add an optional resistor to fix R10 value on bluepill, as documented on http://wiki.stm32duino.com/index.php?title=Blue_Pill
    [morpheus.sch]
2018-08-26 Various changes
    Squeezed board length so it's 10cm long.
    Added polarity indicators to headers.
    Changed name of screw terminals.
    Added diode to LM1117 input.
    Added SDSS pin.
    [morpheus.sch]
2019-01-25 Prepare branch for (coming soon) KiCAD rework.
    [morpheus.sch]
2019-07-12 Add KiCAD based version
    Add KiCAD based version. Hopefully this will allow people to modify the board easier than with gEDA.
    [Morpheus-kicad.kicad_pcb, Morpheus-kicad.sch]
2019-07-12 Add documents
    Add the usual templates for etching the board, plus BOM, schematics and render pictures.
    [components.xlsx]
2019-08-14 Add reverse current protection
    Added a 1N4007 or similar diode to protect from reverse current. Bear in mind that, without a fuse, it will just burn and let current pass again, damaging components.
    [Morpheus-kicad.kicad_pcb, Morpheus-kicad.sch]
2019-08-14 Update readme
    Added reverse current protection. Also, Marlin (2.0) has a new feature in which you can set thermistor values directly, so a new table isn't needed.
2019-11-20 Add header
    Added a header for the unused pins, just to make them usable.
    [Morpheus-kicad.kicad_pcb, Morpheus-kicad.sch]
2020-04-16 Modified headers and added teardrops
    Re-organized J5 and J6 headers, and added teardrops on all pads, which helps a lot with home etching.
    Also, after seeing some people who needed an external USB port, I added a small header to take out the USB data lines without changing the whole board.
    [Morpheus-kicad.sch]

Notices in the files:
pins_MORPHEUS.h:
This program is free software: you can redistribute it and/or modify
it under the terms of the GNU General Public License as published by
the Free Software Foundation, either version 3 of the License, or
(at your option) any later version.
